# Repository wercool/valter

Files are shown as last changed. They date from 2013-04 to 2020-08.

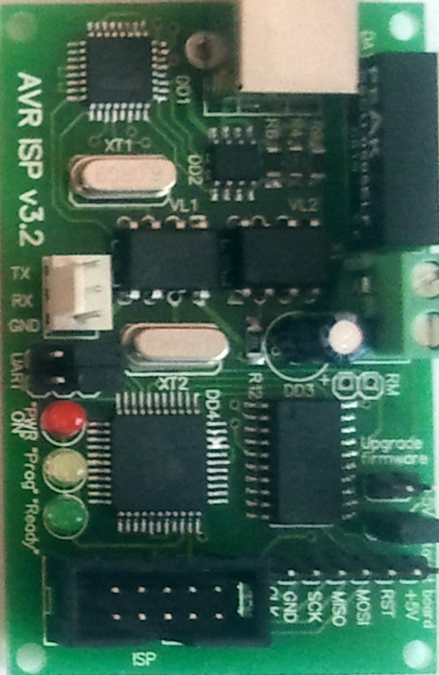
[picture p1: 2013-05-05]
mechanics/textures/avr_programmer.jpg

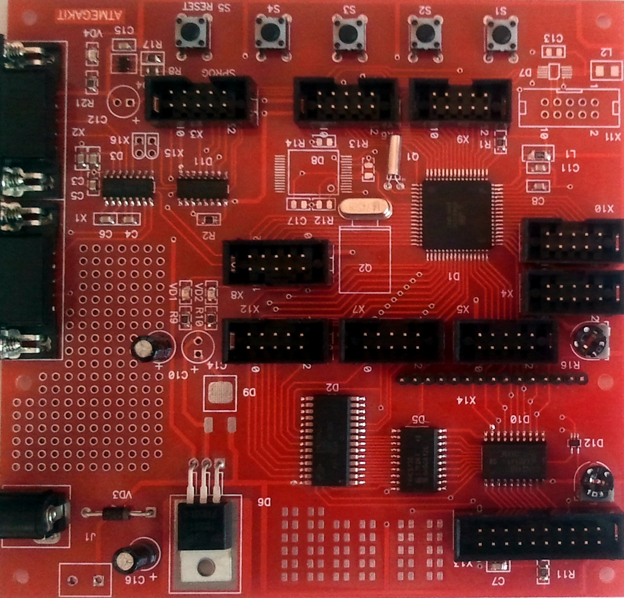
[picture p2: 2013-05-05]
mechanics/textures/mega128.jpg

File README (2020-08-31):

TRIOLAN IP: 109.87.34.156

============
Project Tree
============
cybernetics/*                               [generalized schemes, flowcharts and graphs of the whole project and it's parts, relational diagrams and schemes, etc.]
electronics/*                               [electronic and electric circuits, schemas, graphs, flowchart, abstractions, etc.]
electronics/circuits/*                      [electronic and electric principal circuits]
electronics/circuits/libcomponents/*        [Proteus library components]
electronics/circuits/libcomponents/src/*    [Proteus library components editable source Proteus files]
electronics/circuits/simulations/*          [Proteus circuits simulations]
electronics/circuits/pcb/*                  [pcb for printing and manufacturing]
electronics/flowcharts/*                    [schemas, graphs, flowchart, abstractions]
electronics/documents/*                     [data sheets on the utilized components, modules, other parts]
electronics/tables/*                        [tables of parts, pinouts, input/outputs, troubleshooting tables, etc.]
mechanics/*                                 [mechanical parts and assemblies produced in SolidWorks only]
software/*                                  [all program code assemblies and utilities, core "meta" OS, all code sources for all programmable devices like computer, microcontroller, etc.]
software/documents/*                        [miscellaneous software related documents]
software/microcontroller/*                  [microcontroller source codes and binaries]
software/microcontroller/AVR                [Atmel AVR mc source codes and binaries]
software/microcontroller/ARM                [Atmel ARM mc source codes and binaries]
software/computer/*                         [pc source codes and binaries]
software/computer/client/*                  [pc source codes and binaries - client control applications]
software/computer/client/qt                 [pc source codes for main Experimental Valter's Client Application done in Qt]
software/computer/server/*                  [pc source codes and binaries - embedded programs, core application for robot]
software/computer/server/core/*             [core application for robot (meta OS)]
software/computer/server/www/*              [web applications]

=============
Project Tools
=============
For mechanics:
1.SolidWorks 2013 x64 Edition

For electronics:
1.Proteus 7.10 SP0

For flowcharts:
1.Dia 0.97.2

For documents:
1.LibreOffice 4.0

For graphics:
1.GIMP 2

--------------------------------------------------------------------------------------------------------------------

07.10.2015 Moved to GitHub

--------------------------------------------------------------------------
07.10.2015 Confirmed
31.08.2020 Confirmed

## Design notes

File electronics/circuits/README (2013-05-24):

ussensorboard.DSN
In-home made board with US Sensors (T and R), terminal for Sharp IR distance sensor, terminals for navigation signal LEDs.

foiled fiberglass: 90x215 (2 pcs), 112x360, 37x250

platform control p1:

INPUTS:
mainAccumulatorVoltage
leftAccumulatorVoltage
rightAccumulatorVoltage
mainAccumulatorAmperageTOTAL
mainAccumulatorAmperageBOTTOM
mainAccumulatorAmperageTOP
leftAccumulatorAmperage
rightAccumulatorAmperage
chargerVoltage
leftMotorCS
rightMotorCS
turretMotorCS
turretAngle

leftMotorDIAGa
leftMotorDIAGb
rightMotorDIAGa
rightMotorDIAGb
turretMotorDIAGa
turretMotorDIAGb
leftMotorCnt
rightMotorCnt

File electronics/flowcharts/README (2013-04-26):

Platform.p1.dia
===============
Left Motor Driver
Right Motor Driver
Left Motor Optical Encoder
Right Motor Optical Encoder
Left Motor USB-Mouse Encoder
Right Motor USB-Mouse Encoder
US wall sensors
IR wall sensors

Platform.p2.dia
===============
60Ah Accumulator Sensors
5Ah Left Accumulator Sensors
5Ah Right Accumulator Sensors
Acid Accumulator Charger

Platform.cap.dia
================
Turret Motor Diver
Turret position
Left and Right sonar

Manipulator.dia
===============
Manipulator motors and sensors

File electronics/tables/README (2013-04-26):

Manipulator.ods
This file contains distribution of pins between BIT IN/OUT, ADC, and PWM targets/sources.
See electronics/flowcharts/Manipulator.dia for reference.

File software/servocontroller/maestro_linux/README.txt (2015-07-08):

Pololu Maestro USB Servo Controller Linux Software

Release Date: 2010-05-07
http://www.pololu.com/

== Summary ==

This binary release contains the Maestro Control Center
(MaestroControlCenter) and the Maestro command-line utility
(UscCmd).  These programs allow you to configure and control the
Maestro over USB.

== Prerequisites ==

You will need to download and install these packages:

  libusb-1.0-0-dev mono-runtime libmono-winforms2.0-cil

In Ubuntu, you can do this with the command:

  sudo apt-get install libusb-1.0-0-dev mono-runtime libmono-winforms2.0-cil

== USB Configuration ==

You will need to copy the file 99-pololu.rules to /etc/udev/rules.d/
in order to grant permission for all users to use Pololu USB devices.
If you already plugged in a Pololu USB device, you should unplug it at
this point so the new permissions will get applied later when you plug
it back in.

== Running the programs ==

You can run the programs by typing one of the following commands:

   ./MaestroControlCenter
   ./UscCmd

If you get an error message that says "cannot execute binary file",
then try running the program with the mono runtime, for example:

   mono ./UscCmd

== Source Code ==

The C# source code for UscCmd is available in the Pololu USB Software
Development Kit, available at:

  http://www.pololu.com/docs/0J41

== Text Display Problem in Ubuntu 9.10 ==

If you run MaestroControlCenter and some of the UI text is missing,
your problem might be caused by a bug in a graphics driver that comes
with Ubuntu 9.10 (Karmic Koala).

The driver is in the package xserver-xorg-video-intel.  The driver is
for the Intel i8xx and i9xx family of chipsets, including i810, i815,
i830, i845, i855, i865, i915, i945 and i965 series chips.  You can see
if your computer has one of those chipsets by running `lspci` and
finding your graphics card.

Version 2.9.0 of the driver is known to have a bug.
Upgrading to Version 2.9.1 seems to fix the bug.

You can determine what version of the driver you have by running:

  dpkg -l | grep xserver-xorg-video-intel

You can determine what version of the driver your X.org server is
actually using by looking in /var/log/Xorg.0.log for a message like:

  (II) Module intel: vendor="X.Org Foundation"
          compiled for 1.6.4, module version = 2.9.1
          Module class: X.Org Video Driver
          ABI class: X.Org Video Driver, version 5.0

One way to fix the problem is to compile the new version of the driver
(2.9.1) from source and use it.  Here are the instructions for doing
that:

1) Go to http://xorg.freedesktop.org/archive/individual/driver/
   and get the latest version of the xf86-video-intel driver.
   At the time of this writing (2009-12-23), the latest version
   was xf86-video-intel-2.9.1.tar.gz.

2) Unzip the archive and install the archive by running:

     tar -xzvf xf86-video-intel-2.9.1.tar.gz

3) Install the required dev packages:

     sudo apt-get install xserver-xorg-dev libdrm-dev x11proto-gl-dev x11proto-xf86dri-dev

4) Install the driver by running:

     cd xf86-video-intel-2.9.1
     ./configure
     make
     sudo make install

   This installs the drivers to /usr/local/lib/xorg/modules/drivers,
   but that is not the location where the X.org server searches for
   drivers.

5) (Optional) Make a backup up the existing drivers so that if
   something goes wrong you can revert to them:
     cp -Ri /usr/lib/xorg/modules/drivers ~/backup_xorg_drivers
 
6) Close all of your graphical applications and log out because we must
   temporarily shut down the Gnome Desktop Manager (gdm).

7) Go to a text console by pressing Ctrl+Alt+F1 or Ctrl+Alt+F2.

8) Run these commands:
     sudo service gdm stop
     sudo cp /usr/local/lib/xorg/modules/drivers/* /usr/lib/xorg/modules/drivers
     sudo service gdm start

9) You should see the Ubuntu log-in screen appear.  If it does not, try
   pressing Ctrl+Alt+F7.  The graphic driver bug should now be fixed!

For more information, see:
https://bugzilla.novell.com/show_bug.cgi?id=549882
https://bugs.launchpad.net/ubuntu/+source/xserver-xorg-video-intel/+bug/462349
http://intellinuxgraphics.org/

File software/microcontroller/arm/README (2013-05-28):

On 64 bits version install 32 bits libraries: 

apt-get install ia32-libs

==============

ia32-libs - ia32 shared libraries - transitional package
ia32-libs-multiarch - Multi-arch versions of former ia32-libraries

Useful links:

AT91 ARM-Projects
http://www.siwawi.arubi.uni-kl.de/avr_projects/arm_projects/index_at91.html

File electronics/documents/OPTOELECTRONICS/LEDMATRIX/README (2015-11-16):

missed dimension on the drawing: 24.6mm (between pins axis - 24.1mm)

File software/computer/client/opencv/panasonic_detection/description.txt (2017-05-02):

Panasonic Wireless Phone
cascade_r.xml=Right Oriented
cascade_l.xml=Left Oriented
cascade_t.xml=Top Oriented
cascade_b.xml=Bottom Oriented

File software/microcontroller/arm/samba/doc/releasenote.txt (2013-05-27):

Release Notes ¡V SAM-BA
-----------------------
Release version: 2.11
Release date: 2011

1 Overview

The SAM Boot Assistant (SAM-BA) software provides a means of easily 
programming different Atmel AT91SAM devices. They are based on a common 
dynamic linked library (DLL), the sam-ba.dll. SAM-BA use the DLL to 
communicate with the target board.

You are strongly recommended to read through the following release notes 
before completing the installation of SAM-BA v2.11.

AT91BOOT_DLL.DLL and SAM-PROG is not updated in this revision. 
SAM-PROG will remain available in  the at91isp v1.13. 
Customer who still wants SAM-PROG can download AT91-ISP v1.13.

----------
2 Downloading and Installing
----------------------------
The software can be found and downloaded from ATMEL's website at 
http://www.atmel.com/dyn/products/tools_card_v2.asp?tool_id=3883
  
- sam-ba_2.11.exe (current release) for Windows
  Install files for the SAM-BA package. 
  Execute sam-ba_2.10.exe to install. 
  
- sam-ba_2.11.zip (current release) for Linux
  Install files for the SAM-BA package only. Uses standard CDC driver
  Unzip the package zip file under a local folder on your PC.

3 Contents
-----------

- sam-ba.dll v1.00 (A dynamic linked library connects AT91SAM-based targets 
  through a USB, JTAG or COM port).

- Segger JLINKARM.DLL V4.28b (DLL for using J-Link / J-Trace with third-party 
  programs JTAG driver)

- TCL Toolchain including tclsh can be downloaded from the following URL:
  http://www.activestate.com/Products/ActiveTcl/

- Documents
  - SAM-BA User Guide.pdf
  - Releasenote.txt
  - readme.txt
  - usb_notice.html

- New features.
  - at91sam3s8 at91sam3s16 support
  - at91sam3x8 at91sam3x4 at91sam3x2 support
  - at91sam9g15 at91sam9g25 at91sam9g35 at91sam9x25 at91sam9x35 support
  - at91sam9n12 support

- SAMBA 2.11 supports the following AT91SAM based microcontrollers:
  - at91sam3s16 at91sam3s8 at91sam3s4 at91sam3s2 at91sam3s1
  - at91sam3u4 at91sam3u2 at91sam3u1
  - at91sam3n4 at91sam3n2 at91sam3n1
  - at91sam3x8 at91sam3x4 at91sam3x2
  - at91sam7a3
  - at91sam7l64 at91sam7l128     
  - at91sam7s161 at91sam7s321 at91sam7s32 at91sam7s64 at91sam7s128 at91sam7s256 at91sam7s512
  - at91sam7se32 at91sam7se256 at91sam7se512
  - at91sam7x128 at91sam7x256 at91sam7x512
  - at91sam7xc128 at91sam7xc256 at91sam7xc512
  - at91sam9260 
  - at91sam9261
  - at91sam9263
  - at91sam9g10
  - at91sam9g15 at91sam9g25 at91sam9g35 at91sam9x25 at91sam9x35
  - at91sam9n12
  - at91sam9g20
  - at91sam9g45
  - at91sam9m10 
  - at91sam9rl64
  - at91sam9xe128
  - at91sam9xe128
  - at91sam9xe256
  - at91sam9xe512
  - at91cap9

4 Bug Fixes and Enhancement
----------------------------
Enhancement:
------------
    - Support USB CDC, JLINK and COM port connection for Vista (32/64) and Windows 7 (32/64)
    - Upgrade to Tcl8.5.9 / Tk8.5.9  (samba 2.10 Tcl8.4.13 / Tk8.4.13)
    - new sam-ba.dll instead of SAMBA_DLL.DLL
    - using usbser.sys(Microsoft Windows USB modem driver system driver file)
      instead of atm6124.sys
    - nandflash applet : Remove RDY/BSY pin usage for SAM-BA
    - remove DDRAM duplicated configurations in board_memories.c 
    - Remove duplicated tcl_lib folder
    - SAM9M10/G45 coherency
    - Add One Wire EEPROM support for sam9x5 series
    - SST Serial Flash support
    - backup connection information and last used folder as soon as sam-ba used
    - add a mask on revision field in JEDEC ID to be able to support several
      version of a given flash
    - Add support of modern Embedded Linux file systems(ubifs / yaffs2 / jffs2 support)
    - Add Jlink speed interface
    - Name of USB serial link
    - TWI Address optional selection for EEPROM (9g15/9g25/9g35/9x25/9x35/9n12)
    - Support /dev/ttyACMx for Linux version samba

Bug Fixes
---------
    - sam3s lowlevel init prevents the user to use a crystal different 
      from 12 MHz
    - the external XTtal shall NOT be enabled for sam9m10
    - descriptor error for SST Serial Flash
    - File compare (>10K) not matched though COM port
    - serial flash driver bug fix
    - sam7x256 flash applet does not write using IAP ROM feature
    - fixed sam7 with IAP flash loader issue
    - fixed sam9m10-g45-ek board_lowlevelinit issue
    - The customer should be allowed to use it's real board name
    - reduce the erase size of serialflash applet
    - No adaptive clocking for SAM3 devices
    - sam7x512 Flash Erase command does not work for the 2nd flash bank
    - Assembly code (in old applets) compilation
    - Wrong lowlevel inits for sam3x applets 
    - Cap9 SDRAM (extram) applet linker script issue
    - Buffer size issue in example samba_dll_usage_VC6
    - Miss "rc" indication in installer, folders and inside the program
    - SAM-BA installer no admin right to install on WIN7 /Vista
    - SAM-BA crashes when no_board selection.
    - SDRAM and DDRAM panes shall not be displayed at the same time in the GUI
    - Nandflash applet debug incorrect info of SEND BOOT FILE
    - Incorrect board name displayed in main window (some board re-target)
    - SAM9G15-ES2 : Cannot be launched twice without cpu reset
    - Name of sam9x25 / x35 tcl files (devices) shall be lowercase
    - TCL scan crash in some case for linux sam-ba
    - After a TCL_Go, If the applet does not return, SAM-BA is frozen.
    - Incorrect board name displayed in main window (some board re-target)
    - Sam9n12 applet compile error in linux
    - Missing ACK for COM connection in extram and lowlevel applet for 9xx5/9n12
    
Known Issues
---------
    - Some boards can't work properly through USB/COM port connection without reseting the board
----------------------------------------------------------------------------------------------------------------------------------

5 History 
---------------------

----------------------------------------------------------------------------------------------------------------------------------
v2.10:
    - Fixed Jtag issue when the chip has booted on a program from an external memory (Nand, DF ...) and if that program has initialized the PLL and MCK. 
    - Fixed Jtag issue if customers not running the chips with the same XTAL or external oscillator as on our EK boards.
    - Add new at25 device AT25DF512B-SSH-B,AT25DF021-SSH-B,AT25DF021-MH-T,AT25DF161-SSH-B,AT25DF161-SH-B,AT25DF641-S3H-B.
    - Fixed flash init problem on AT91SAM7S32/321.
    - Fixed DataFlash init problem on AT91SAM7A3.
    - Fixed dataFlash programming of large files fails (~>1Mbytes) on AT91SAM9G20 with COM port connection.
    - Fixed flash applet initialization in CDC mode on SAM7.
    - Fixed SAM7X/XC access cdc linux , Flash init fail with error message.
    - Add "Send Boot File" for SAM9G10/G20/G45/M10 chips.
    - Add lowlevel_init in flash applet for sam7 chip.
    - Fix spell error "appletMAilboxAddr" at91sam7s128-ek.tcl.
    - Fix security bit script for at91sam3u4-ek.tcl.
    - Fixed  Nand flash program algorithm for SAM9M10/9G45.
    - When using the JTAG it is not possible to program the 2nd flash bank of the SAM7X512 device.
    - Fixed flash init problem on AT91SAM7S32/321.
    - Add support to verify if an existing sam-ba task is running before launching sam-ba, ask to kill it.
    - No Support for 8-bit Nand Small Blocks. The algorithm is not correctly implemented for such nandflash devices.
    - An incorrect EEPROM::appletAddr in TCL definitions address to SDRAM could lead to crash for some at91sam9 boards.
    - The applet initialization does not report any error in case no EEPROM is connected or an EEPROM different from the selected one 
      is Enabled by the script.
    - Latest large nandflash devices have bigger page size (4K for instance) and SAMBA and the SW library does not support it. This 
      may be due to the new spare zone organization.
    - An incorrect 'Enable Security Bit' descriptor for SAM3U.
    - Add function to erase blocks for NAND flash applet (command line only)
    - NOR flash not able to 'erese all' on sam9m10-g45-ek REV.A board
    - When SAM-BA starts, it could not differentiate a real invalid ID from a communication error with the chip.
    - Sam-ba could not detect real board, if user select a wrong board name from drop list.
    - It is not possible to connect to SAMBA with a SAM9260-EK using the RS232 port.
    - Some customer board could not program dataflash properly, improve the programming algorithm.
    - Improved erase all algorithm for nandflash applet. Fixed Usb/com timeout problem on some 8-Bit Nand flash.
    - Fixed eeprom program algorithm for SAM9260-EK.
    - Add Dataflash (SPI0 CS3) support for SAM9261-EK.
    - Flash applet in command mode could not unlock region before write.
    - Fixed connection on SAM3S-EK with COM port.
    - CDC version hang during flash init of SAM7 chips.
    - Connect/disconnect functionality support.

----------------------------------------------------------------------------------------------------------------------------------
v2.9:
    - Added support for AT91SAM9M10, AT91SAM9G45, AT91SAM9G10, AT91SAM7SL.
    - Added support for AT91SAM3U, with USB and COM port connection only (no SAM-ICE).
    - Fixed Dataflash access on AT91SAM9G20 CU-A.
    - Select 16/32 bits external SDRAM in board TCL file without applet compilation.
    - External memory initialization failure at SAM-BA startup is indicated by a popup
       window, but user can choose to use SAM-BA anyway.
    - Added a listbox to choose applet debug traces level easily. Traces are sent to DBGU
       port when using USB or JTAG connection link.
    - Added Nandflash bad block listing script.
    - Added a document to help user to customize SAM-BA and applets for a custom board.

----------------------------------------------------------------------------------------------------------------------------------
v2.8:
    - Added support for DataFlash in Binary mode (Power of 2 page size),
    - Improved programing speed with applets running at higher CPU and MCK clock frequency,
    - Fixed AT91SAM7L64/128 support,
    - Fixed AT91SAM7XC support.

----------------------------------------------------------------------------------------------------------------------------------
v2.7:
    - New flash programming applets :
        - NandFlash, DataFlash, SerialFlash, NorFlash,
        - GCC code,
        - based on at91lib software library. 
    - Added support for AT91SAM7L64/128, AT91SAM9G20, AT91SAM9XE,
        and AT91CAP9 (EK and STK).
    - Fixed AT91SAM9RL64 support.

----------------------------------------------------------------------------------------------------------------------------------
v2.6:
    - Fixed AT91SAM9263 DataFlash script bug.
    - Fixed AT91SAM7S512/SE512/X512 Flash programming bug.
    - Fixed AT91SAM7SE/X/XC GPNVM accesses with JTAG.
    - Added support for AT91SAM9RL64 and AT91CAP9.
    - More NandFlash supported :
        * Micron, Samsung, Toshiba, Fujitsu, National, and STMicro
        * 1Gbit to 16Gbits, 8 and 16 bits bus size.
    - Improved NandFlash bad block management (Skip block method).
    - JTAG support for AT91SAM926x.

----------------------------------------------------------------------------------------------------------------------------------
v2.5:
    - Bypass of Connection Message Box when launching SAM-BA with port
       and board name in command line parameter.
    - Support for AT91SAM9XE family.
    - Various bug fixes : script mode feature improved (no more message boxes),
       open and save file dialog boxes displays now correctly.

----------------------------------------------------------------------------------------------------------------------------------
v2.4:
    - J-Link support improved for AT91SAM7A3
    - AT91SAM9263 NandFlash block programming support
    - Added SDRAM config for 48, 100 and 133 MHz MCK on SAM926x boards
    - Minor GUI bug fixes

----------------------------------------------------------------------------------------------------------------------------------
v2.3:
    Supports:
    - SAM7S32/321/64/128/256/512
    - SAM7X(C)128/256/512
    - SAM7SE32/256/512
    - SAM9260/9261/9263
    Only by adding/modifying TCL scripts in the lib directory, it is now
      possible to add:
    - Your own boards
    - Your own memory algorithms
----------------------------------------------------------------------------------------------------------------------------------

6 Contact Information
---------------------
For support on the AT91 Software Package please send request to at91@atmel.com

---------------------
6 Copyright (c) 2011, Atmel Corporation All rights reserved.

 * ----------------------------------------------------------------------------
 *         ATMEL Microcontroller Software Support
 * ----------------------------------------------------------------------------
 * Copyright (c) 2011, Atmel Corporation
 *
 * All rights reserved.
 *
 * Redistribution and use in source and binary forms, with or without
 * modification, are permitted provided that the following conditions are met:
 *
 * - Redistributions of source code must retain the above copyright notice,
 * this list of conditions and the disclaimer below.
 *
 * Atmel's name may not be used to endorse or promote products derived from
 * this software without specific prior written permission.
 *
 * DISCLAIMER: THIS SOFTWARE IS PROVIDED BY ATMEL "AS IS" AND ANY EXPRESS OR
 * IMPLIED WARRANTIES, INCLUDING, BUT NOT LIMITED TO, THE IMPLIED WARRANTIES OF
 * MERCHANTABILITY, FITNESS FOR A PARTICULAR PURPOSE AND NON-INFRINGEMENT ARE
 * DISCLAIMED. IN NO EVENT SHALL ATMEL BE LIABLE FOR ANY DIRECT, INDIRECT,
 * INCIDENTAL, SPECIAL, EXEMPLARY, OR CONSEQUENTIAL DAMAGES (INCLUDING, BUT NOT
 * LIMITED TO, PROCUREMENT OF SUBSTITUTE GOODS OR SERVICES; LOSS OF USE, DATA,
 * OR PROFITS; OR BUSINESS INTERRUPTION) HOWEVER CAUSED AND ON ANY THEORY OF
 * LIABILITY, WHETHER IN CONTRACT, STRICT LIABILITY, OR TORT (INCLUDING
 * NEGLIGENCE OR OTHERWISE) ARISING IN ANY WAY OUT OF THE USE OF THIS SOFTWARE,
 * EVEN IF ADVISED OF THE POSSIBILITY OF SUCH DAMAGE.
 * ----------------------------------------------------------------------------

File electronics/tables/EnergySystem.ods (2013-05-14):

BIT IN | 5 | 5 from SM 1236 charger
BIT OUT | 6
ADC | 3

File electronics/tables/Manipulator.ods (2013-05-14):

BIT IN | 1
BIT OUT | 14
ADC | 8 | 7 in case of series connection of left upper right sensors
PWM | 3 (4) | 4 in case of camera servo control from mc

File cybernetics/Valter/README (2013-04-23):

http://en.wikipedia.org/wiki/Cybernetics
http://ru.wikipedia.org/wiki/Кибернетика

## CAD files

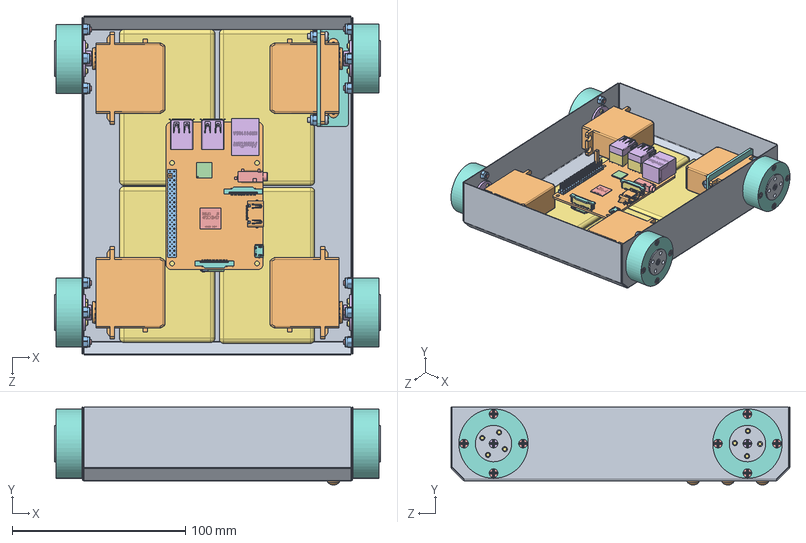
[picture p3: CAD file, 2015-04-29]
documents/GB-0814/mechanics/GB0814.SLDASM
188.0 x 44.8 x 195.4 mm
case.bottom
SM4315R x 4
raspberry_pi_B+_(bar_180_2x20)
raspberry_pi_B+_(QFN64)
raspberry_pi_B+_(168_FBGA_12x12)
raspberry_pi_B+_(USB_x2_part1) x 2
raspberry_pi_B+_(USB_x2_part2) x 2
raspberry_pi_B+_(micro_USB_cover)
raspberry_pi_B+_(micro_USB_contacts)
raspberry_pi__HDMI_socket_cover
raspberry_pi__HDMI_socket_inside
raspberry_pi__HDMI_socket_large_pin x 10
raspberry_pi__HDMI_socket_small_pin x 9
raspberry_pi_B+_(RJ45)
raspberry_pi__15_pin_FFC_Connector_body x 2
raspberry_pi__15_pin_FFC_Connector_locker x 2
raspberry_pi__15_pin_FFC_Connector_pins x 30
raspberry_pi_B+_(CI_Board)
raspberry_pi_B+_(microsd_slot2)
raspberry_pi_B+_(microsd2)
raspberry_pi_B+_(audio_video2)
SM4315R.horn x 4
accumulator x 4
flange x 4
wheel.hub x 4
pin.2.54.holder
self.stop.nut.m3 x 20
ball.4mm x 152
m3.screw.18mm x 16
m3.screw.30mm x 4
m2.screw x 16
servo.fixture
m3.screw.10mm x 4
4mm.rivet x 3

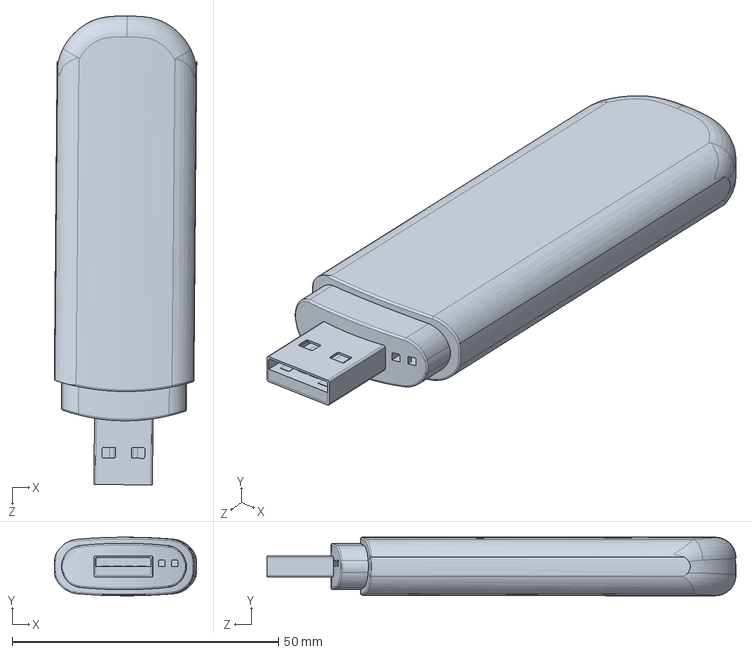
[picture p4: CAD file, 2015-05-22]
documents/misc/GB-0814/mechanics/3gmodem/3gmodem.SLDASM
26.7 x 11.0 x 88.0 mm

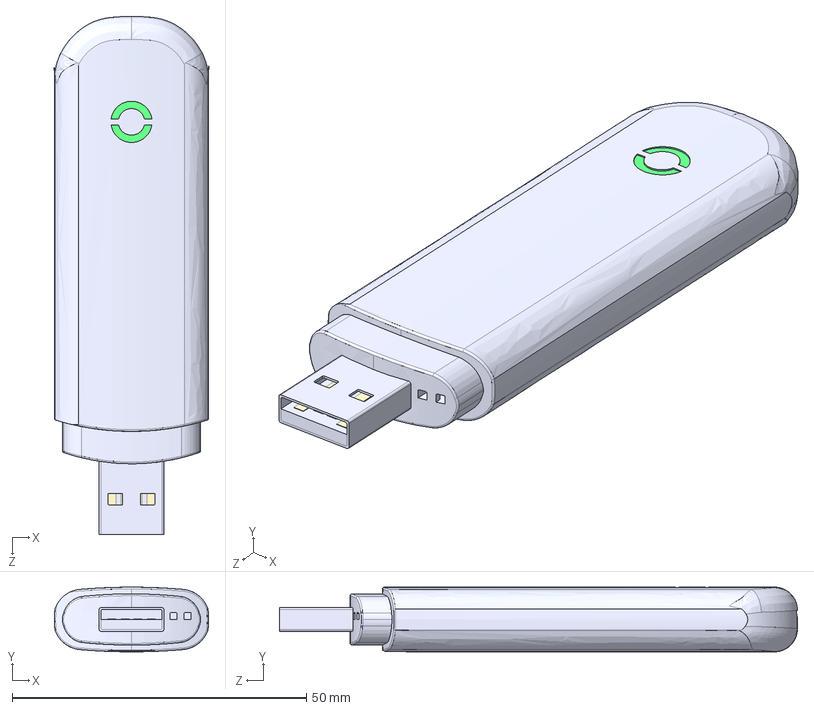
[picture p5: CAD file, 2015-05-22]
documents/misc/GB-0814/mechanics/3gmodem/IGES Files/Main_IGES.IGS
26.2 x 11.0 x 88.0 mm

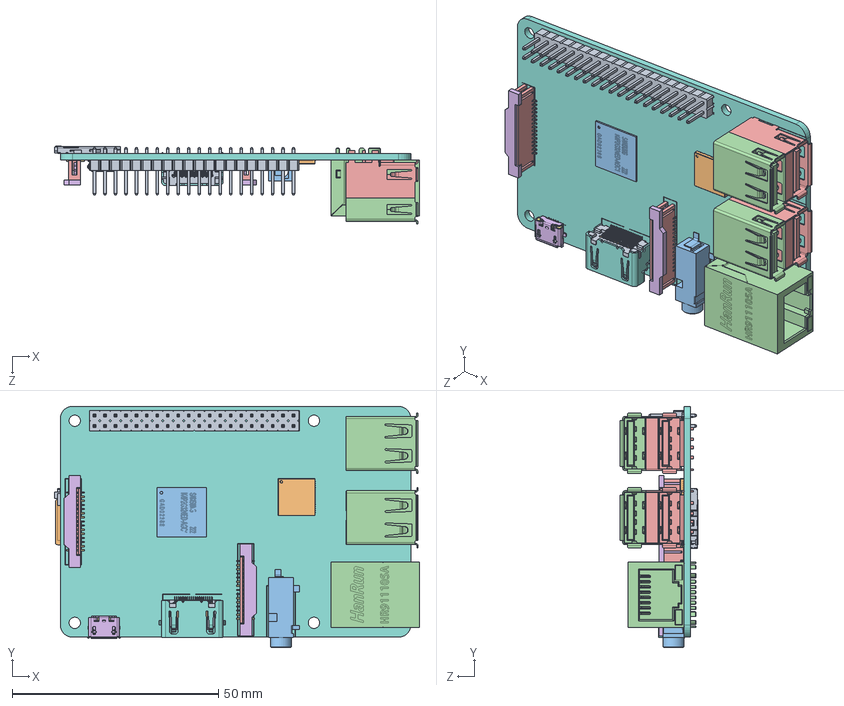
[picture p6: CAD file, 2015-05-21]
documents/misc/GB-0814/mechanics/raspberry-pi-model-b-2/raspberrypi_b_+_(assembly).SLDASM
88.5 x 58.5 x 18.9 mm
raspberry_pi_B+_(bar_180_2x20)
raspberry_pi_B+_(QFN64)
raspberry_pi_B+_(168_FBGA_12x12)
raspberry_pi_B+_(USB_x2_part1) x 2
raspberry_pi_B+_(USB_x2_part2) x 2
raspberry_pi_B+_(micro_USB_cover)
raspberry_pi_B+_(micro_USB_contacts)
raspberry_pi__HDMI_socket_cover
raspberry_pi__HDMI_socket_inside
raspberry_pi__HDMI_socket_large_pin x 10
raspberry_pi__HDMI_socket_small_pin x 9
raspberry_pi_B+_(RJ45)
raspberry_pi__15_pin_FFC_Connector_body x 2
raspberry_pi__15_pin_FFC_Connector_locker x 2
raspberry_pi__15_pin_FFC_Connector_pins x 30
raspberry_pi_B+_(CI_Board)
raspberry_pi_B+_(microsd_slot2)
raspberry_pi_B+_(microsd2)
raspberry_pi_B+_(audio_video2)

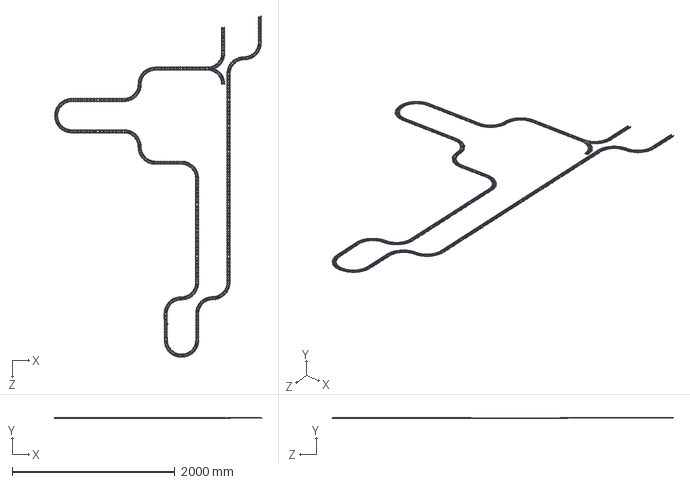
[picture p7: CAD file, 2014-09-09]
documents/misc/railway/railway.SLDASM
2545.2 x 6.78 x 4186.4 mm
linear.rail x 23
radius.rail x 17

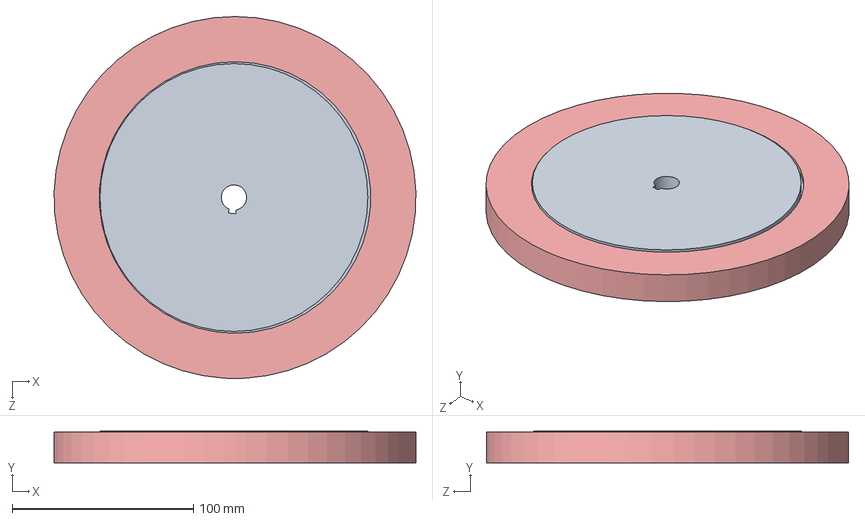
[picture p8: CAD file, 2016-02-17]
mechanics/turret.SLDASM
199.9 x 17.6 x 200.0 mm
turret-p1
turret-p2 x 17
turret-p3
turret-p5 x 100
turret-p4

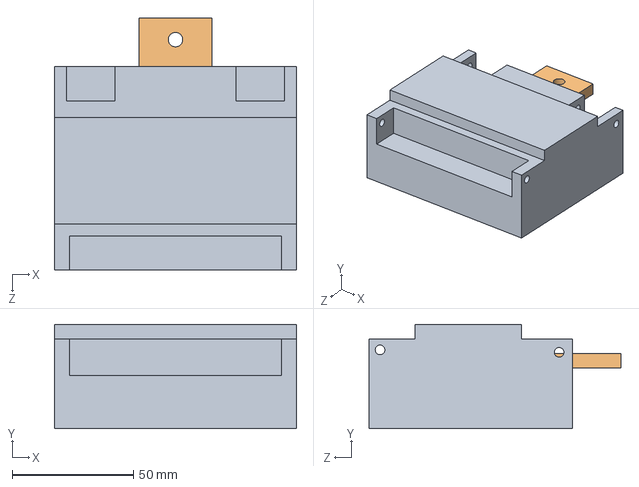
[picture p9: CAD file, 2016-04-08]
software/ros/misc/models/valter/swmodel/palm.SLDASM
100.0 x 43.0 x 104.0 mm
palm
palm.p1

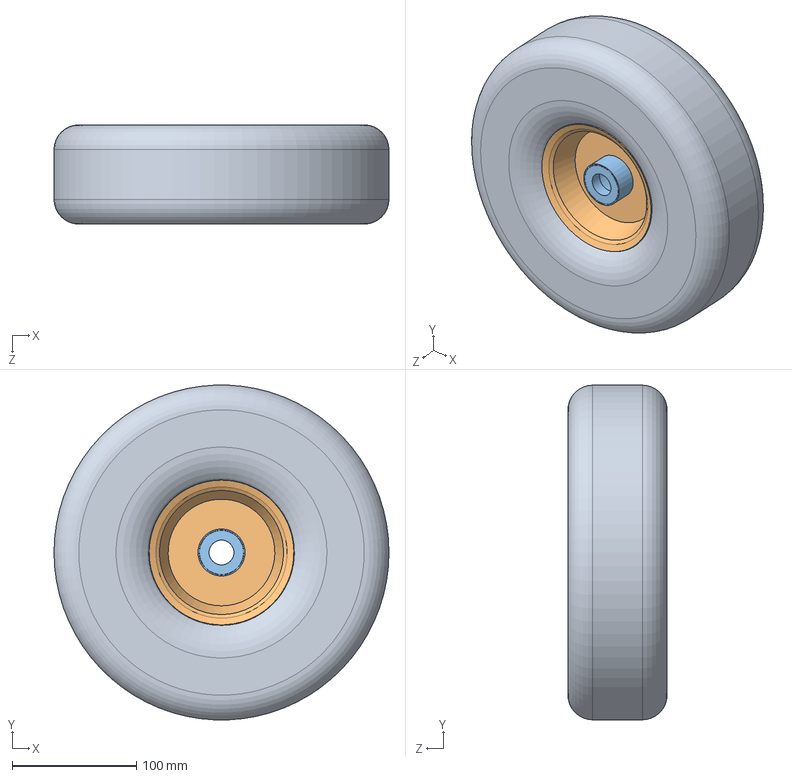
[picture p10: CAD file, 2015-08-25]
software/ros/misc/models/valter/swmodel/wheel/wheel.SLDASM
270.0 x 269.8 x 80.0 mm
wheel.chamber
wheel.metal.front
wheel.metal.internal

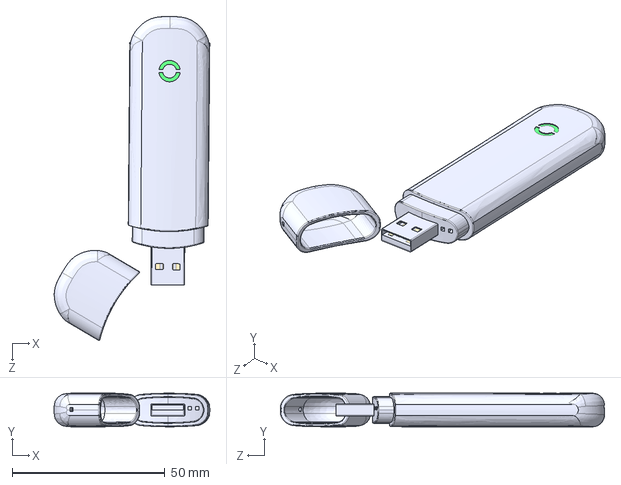
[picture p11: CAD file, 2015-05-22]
documents/misc/GB-0814/mechanics/3gmodem/IGES Files/Dongle Assembly_IGES.IGS
51.0 x 11.0 x 106.2 mm

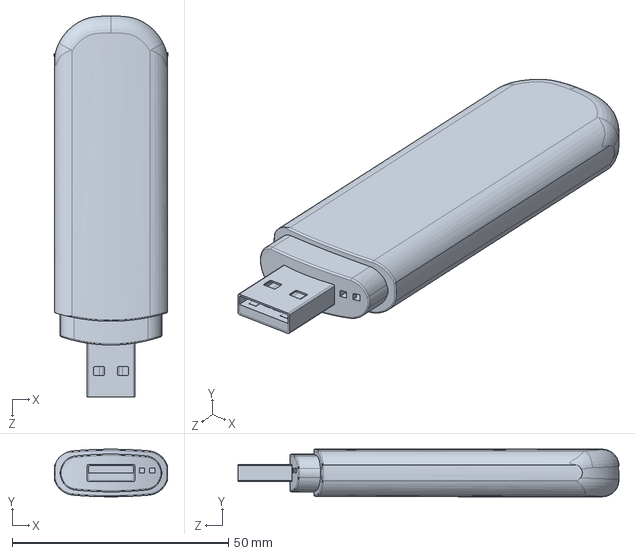
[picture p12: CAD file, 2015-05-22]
documents/misc/GB-0814/mechanics/3gmodem/Main.SLDPRT
26.2 x 11.0 x 88.0 mm

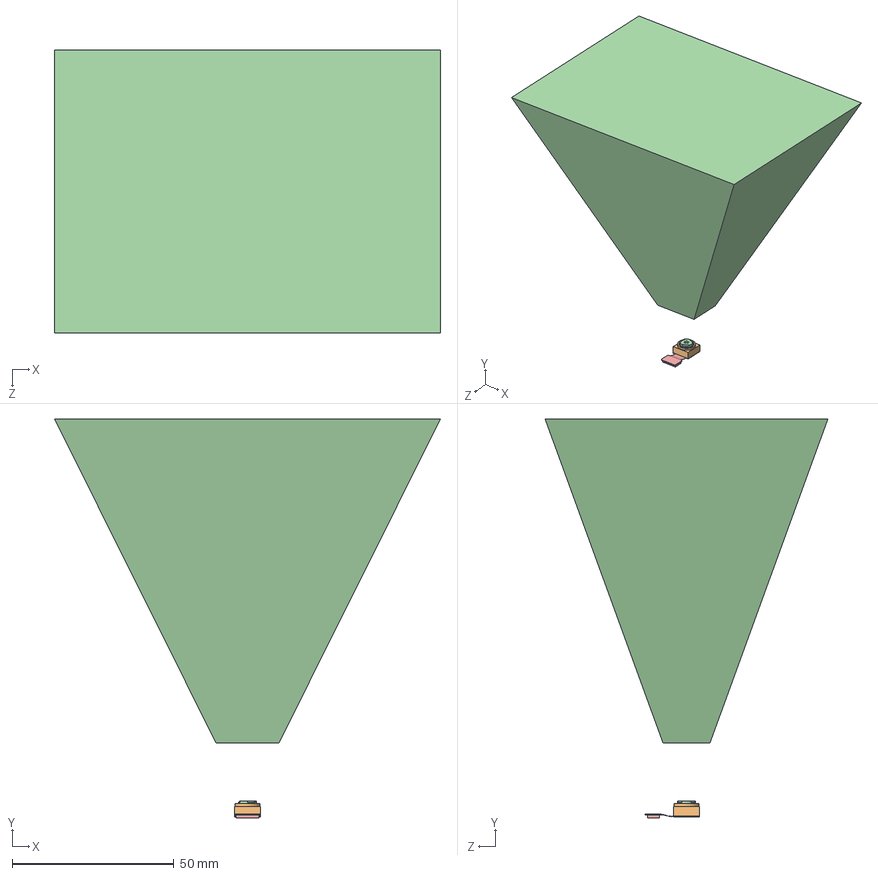
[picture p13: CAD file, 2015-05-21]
documents/misc/GB-0814/mechanics/raspberry-pi-camera/OVA5647.SLDASM
119.2 x 123.2 x 87.4 mm
OVA5647
OVA5647_Housing
OVA5647_IR-Glas
OVA5647_Lens
OVA5647_Pigtail

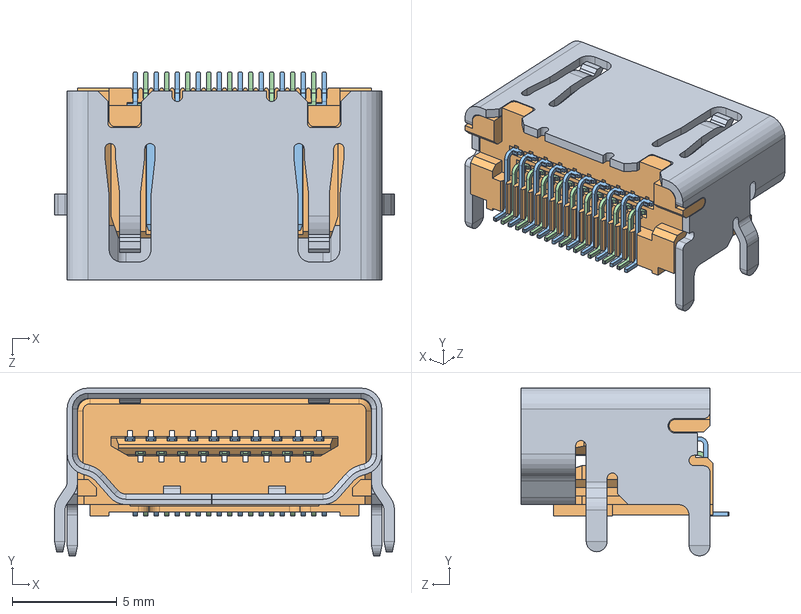
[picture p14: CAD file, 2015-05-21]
documents/misc/GB-0814/mechanics/raspberry-pi-model-b-2/raspberry_pi_B+_(HDMI_socket).SLDASM
16.2 x 8.00 x 9.90 mm
raspberry_pi__HDMI_socket_cover
raspberry_pi__HDMI_socket_inside
raspberry_pi__HDMI_socket_large_pin x 10
raspberry_pi__HDMI_socket_small_pin x 9

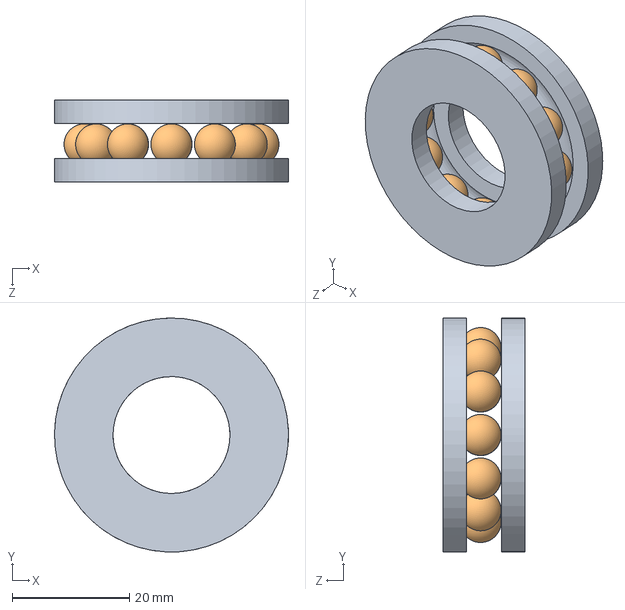
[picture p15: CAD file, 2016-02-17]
mechanics/wheel.stop.bearing.SLDASM
40.0 x 40.0 x 14.0 mm
wheel.stop.bearing.p1 x 2
wheel.stop.bearing.p2 x 12

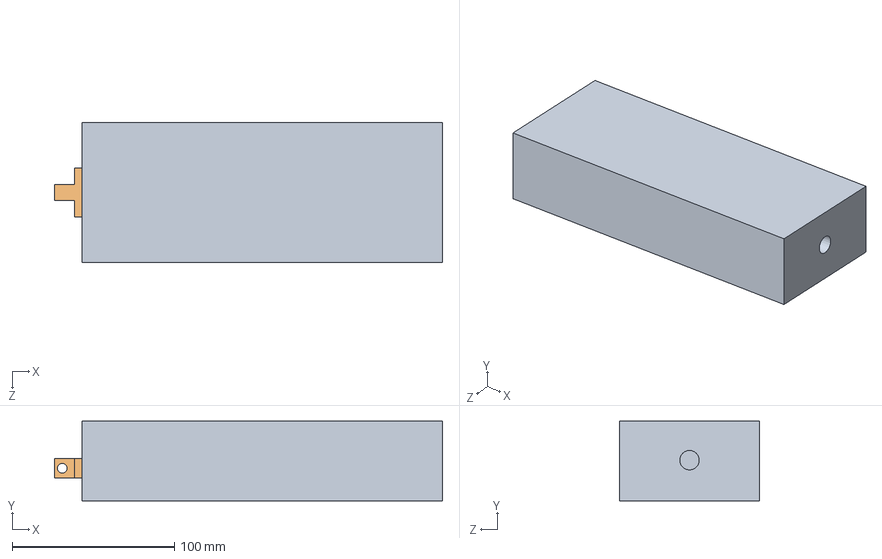
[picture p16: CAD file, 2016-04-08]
software/ros/misc/models/valter/swmodel/forearm.SLDASM
239.0 x 49.0 x 86.0 mm
forearm.p2
palm.lift.fixture

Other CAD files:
documents/misc/GB-0814/mechanics/3gmodem/STL Files/Main_STL.STL
software/ros/misc/models/valter/swmodel/wheel.support/wheel.support.SLDASM
documents/misc/GB-0814/mechanics/3gmodem/Dongle Assembly.SLDASM
documents/misc/GB-0814/mechanics/LEDLamp/LEDLamp.SLDASM
documents/misc/GB-0814/mechanics/3gmodem/Dongle Assembly_AS PART.SLDPRT
documents/misc/GB-0814/mechanics/3gmodem/IGES Files/Lid_IGES.IGS
documents/misc/GB-0814/mechanics/3gmodem/Lid.SLDPRT
documents/misc/GB-0814/mechanics/3gmodem/STL Files/Lid_STL.STL
documents/misc/GB-0814/mechanics/4mm.rivet.SLDPRT
documents/misc/GB-0814/mechanics/4mmx4mm.rivet.SLDPRT
documents/misc/GB-0814/mechanics/4mmx8mm.rivet.SLDPRT
documents/misc/GB-0814/mechanics/LEDLamp/housing.SLDPRT
documents/misc/GB-0814/mechanics/LEDLamp/ledlampnut.SLDPRT
documents/misc/GB-0814/mechanics/SM4315R.SLDPRT
documents/misc/GB-0814/mechanics/SM4315R.horn.SLDPRT
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

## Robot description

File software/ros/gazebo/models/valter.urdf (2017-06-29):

<robot name="valter">
  <link name="Base">
    <inertial>
      <origin xyz="-0.0831283905237907 -8.99639602360447E-05 0.418094636104011" rpy="0 0 0" />
      <mass value="50.0" />
      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
    </inertial>
    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
  </link>
  <link name="RWheel">
    <inertial>
      <origin xyz="-5.908901840046E-18 -0.04 2.77555756156289E-17" rpy="0 0 0" />
      <mass value="3.62031355964479" />
      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
    </inertial>
    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
  </link>
  <joint name="RWheelJoint" type="fixed">
    <origin xyz="0.000341577688738742 -0.153675665570238 0.14" rpy="-6.12303176911189E-17 0 0" />
    <parent link="Base" />
    <child link="RWheel" />
    <axis xyz="0 1 0" />
  </joint>
  <link name="rwheel_centers">
    <inertial>
      <origin xyz="-8.13151629364128E-19 0.032994484499226 0" rpy="0 0 0" />
      <mass value="0.0783773140784392" />
      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
    </inertial>
    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
  </link>
  <joint name="rwheel_centers_fixed" type="fixed">
    <origin xyz="0 -0.00181724367610836 0" rpy="3.14159265358979 0 0" />
    <parent link="RWheel" />
    <child link="rwheel_centers" />
    <axis xyz="0 0 0" />
  </joint>
  <link name="LWheel">
    <inertial>
      <origin xyz="-2.77555756156289E-17 -0.04 2.77555756156289E-17" rpy="0 0 0" />
      <mass value="3.62031355964479" />
      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
    </inertial>
    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
  </link>
  <joint name="LWheelJoint" type="fixed">
    <origin xyz="0.000341577688738742 0.154324334429763 0.14" rpy="6.6286088844449E-17 0.39309481042652 -3.14159265358979" />
    <parent link="Base" />
    <child link="LWheel" />
    <axis xyz="0 -1 0" />
  </joint>
  <link name="lwheel_centers">
    <inertial>
      <origin xyz="-6.93889390390723E-18 -0.032994484499226 -2.77555756156289E-17" rpy="0 0 0" />
      <mass value="0.0783773140784395" />
      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
    </inertial>
    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
  </link>
  <joint name="lwheel_centers_fixed" type="fixed">
    <origin xyz="0 -0.00181724367610836 0" rpy="0 -1.66371525153719E-34 0" />
    <parent link="LWheel" />
    <child link="lwheel_centers" />
    <axis xyz="0 0 0" />
  </joint>
  <link name="support_wheels">
    <inertial>
      <origin xyz="-0.219066879644595 -1.38777878078145E-17 -0.111817164878115" rpy="0 0 0" />
      <mass value="1.30791131979034" />
      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
    </inertial>
    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
  </link>
  <joint name="support_wheels_fixed" type="fixed">
    <origin xyz="0.189234607270609 -0.11129709785824 0.0679256801186866" rpy="1.5707963267949 0 0" />
    <parent link="Base" />
    <child link="support_wheels" />
    <axis xyz="0 0 0" />
  </joint>
  <link name="support_wheels_centers">
    <inertial>
      <origin xyz="-0.219066879644595 -2.77555756156289E-17 0.110556114336065" rpy="0 0 0" />
      <mass value="0.101015328916835" />
      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
    </inertial>
    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
  </link>
  <joint name="support_wheels_centers_fixed" type="fixed">
    <origin xyz="0 0 -0.222438597166117" rpy="0 0 0" />
    <parent link="support_wheels" />
    <child link="support_wheels_centers" />
    <axis xyz="0 0 0" />
  </joint>
  <link name="ManipulatorBase">
    <inertial>
      <origin xyz="0.0757274431880703 -0.00904190076144362 -0.035" rpy="0 0 0" />
      <mass value="0.178834143520891" />
      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
    </inertial>
    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
  </link>
  <joint name="ManipulatorBaseFixed" type="fixed">
    <origin xyz="0.15727 0.035461 0.70704" rpy="1.5708 0 3.1416" />
    <parent link="Base" />
    <child link="ManipulatorBase" />
    <axis xyz="0 0 0" />
  </joint>
  <link name="ManipulatorLink1">
    <inertial>
      <origin xyz="0.00842708530014899 -0.298874962931971 0.0349954696862612" rpy="0 0 0" />
      <mass value="0.478012742893284" />
      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
    </inertial>
    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
  </link>
  <joint name="ManipulatorLink1Joint" type="revolute">
    <origin xyz="0.015824 -0.0090419 0" rpy="3.1416 0 3.1416" />
    <parent link="ManipulatorBase" />
    <child link="ManipulatorLink1" />
    <axis xyz="0 0 -1" />
    <limit lower="-1.5" upper="0" effort="0" velocity="0" />
  </joint>
  <link name="ManipulatorLink2">
    <inertial>
      <origin xyz="-0.00196480942981017 0.348379096758467 0.0349954207736472" rpy="0 0 0" />
      <mass value="0.304515245459477" />
      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
    </inertial>
    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
  </link>
  <joint name="ManipulatorLink2Joint" type="revolute">
    <origin xyz="0.10656 -0.49054 0" rpy="0 0 0" />
    <parent link="ManipulatorLink1" />
    <child link="ManipulatorLink2" />
    <axis xyz="0 0 -1" />
    <limit lower="0" upper="1.5" effort="0" velocity="0" />
  </joint>
  <link name="ManipulatorLink3">
    <inertial>
      <origin xyz="-0.0046525999175398 -0.0219448226910157 0.0349954293087308" rpy="0 0 0" />
      <mass value="0.227882111375496" />
      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
    </inertial>
    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
  </link>
  <joint name="ManipulatorLink3Joint" type="revolute">
    <origin xyz="-0.012962 0.55415 0" rpy="0 0 0" />
    <parent link="ManipulatorLink2" />
    <child link="ManipulatorLink3" />
    <axis xyz="0 0 -1" />
    <limit lower="0" upper="1" effort="0" velocity="0" />
  </joint>
  <link name="ManipulatorLink4">
    <inertial>
      <origin xyz="-2.27324754187949E-05 0.0839540654377264 0" rpy="0 0 0" />
      <mass value="0.42934890554545" />
      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
    </inertial>
    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
  </link>
  <joint name="ManipulatorLink4Joint" type="revolute">
    <origin xyz="0 0.008 0.034995" rpy="0 1.5708 0" />
    <parent link="ManipulatorLink3" />
    <child link="ManipulatorLink4" />
    <axis xyz="0 -1 0" />
    <limit lower="-3" upper="3" effort="0" velocity="0" />
  </joint>
  <link name="GripperL">
    <inertial>
      <origin xyz="0.00297778710330867 0.0871448028863351 -0.00986508075006032" rpy="0 0 0" />
      <mass value="0.0398581317877607" />
      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
    </inertial>
    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
  </link>
  <joint name="GripperLJoint" type="prismatic">
    <origin xyz="0.049892 0.090686 -0.0096825" rpy="3.1416 -6.9389E-17 -3.1416" />
    <parent link="ManipulatorLink4" />
    <child link="GripperL" />
    <axis xyz="-1 0 0" />
    <limit lower="-0.03" upper="0" effort="0" velocity="0" />
  </joint>
  <link name="GripperR">
    <inertial>
      <origin xyz="0.00297778710330867 0.0871448028863351 0.00986508075006029" rpy="0 0 0" />
      <mass value="0.0398581317877607" />
      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
    </inertial>
    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
  </link>
  <joint name="GripperRJoint" type="prismatic">
    <origin xyz="-0.049892 0.090686 -0.0096825" rpy="-4.9087E-21 6.9389E-17 1.0613E-16" />
    <parent link="ManipulatorLink4" />
    <child link="GripperR" />
    <axis xyz="1 0 0" />
    <limit lower="0" upper="0.03" effort="0" velocity="0" />
  </joint>
  <link name="Trunk">
    <inertial>
      <origin xyz="1.9082E-17 0.23891 1.3227E-17" rpy="0 0 0" />
      <mass value="27.438" />
      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
    </inertial>
    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
  </link>
  <joint name="TrunkJoint" type="revolute">
    <origin xyz="-0.01423 0.00097293 0.686" rpy="1.5708 0 0" />
    <parent link="Base" />
    <child link="Trunk" />
    <axis xyz="0 -1 0" />
    <limit lower="-1.5" upper="1.5" effort="0" velocity="0" />
  </joint>
  <link name="Torso">
    <inertial>
      <origin xyz="-5.96337908854803E-05 0.239039736167763 6.11490025281825E-17" rpy="0 0 0" />
      <mass value="12.3493829426964" />
      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
    </inertial>
    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
  </link>
  <joint name="TorsoJoint" type="revolute">
    <origin xyz="0 0.45 0" rpy="0 0 0" />
    <parent link="Trunk" />
    <child link="Torso" />
    <axis xyz="0 0 -1" />
    <limit lower="0" upper="1" effort="0" velocity="0" />
  </joint>
  <link name="Neck">
    <inertial>
      <origin xyz="-2.54485853576885E-05 0.0271590293807542 3.30681662608079E-17" rpy="0 0 0" />
      <mass value="0.264426936484469" />
      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
    </inertial>
    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
  </link>
  <joint name="NeckJoint" type="revolute">
    <origin xyz="-0.00017682 0.42056 0" rpy="0 0 0" />
    <parent link="Torso" />
    <child link="Neck" />
    <axis xyz="0 -1 0" />
    <limit lower="-1.57" upper="1.57" effort="0" velocity="0" />
  </joint>
  <link name="Head">
    <inertial>
      <origin xyz="0.00279372413046049 0.114190295410849 1.01047642475649E-16" rpy="0 0 0" />
      <mass value="5.04298545454377" />
      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
    </inertial>
    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
  </link>
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

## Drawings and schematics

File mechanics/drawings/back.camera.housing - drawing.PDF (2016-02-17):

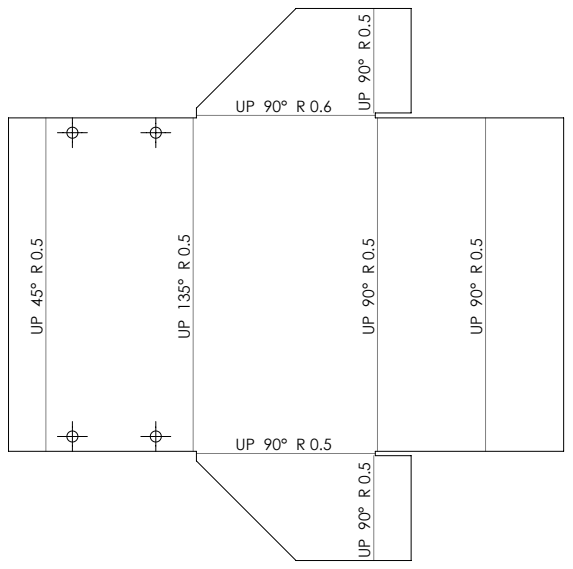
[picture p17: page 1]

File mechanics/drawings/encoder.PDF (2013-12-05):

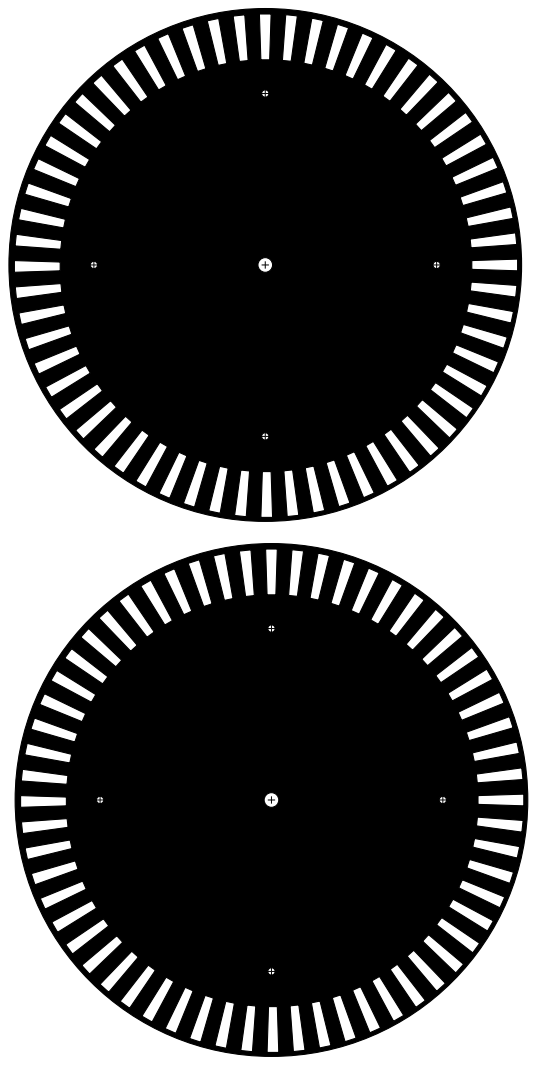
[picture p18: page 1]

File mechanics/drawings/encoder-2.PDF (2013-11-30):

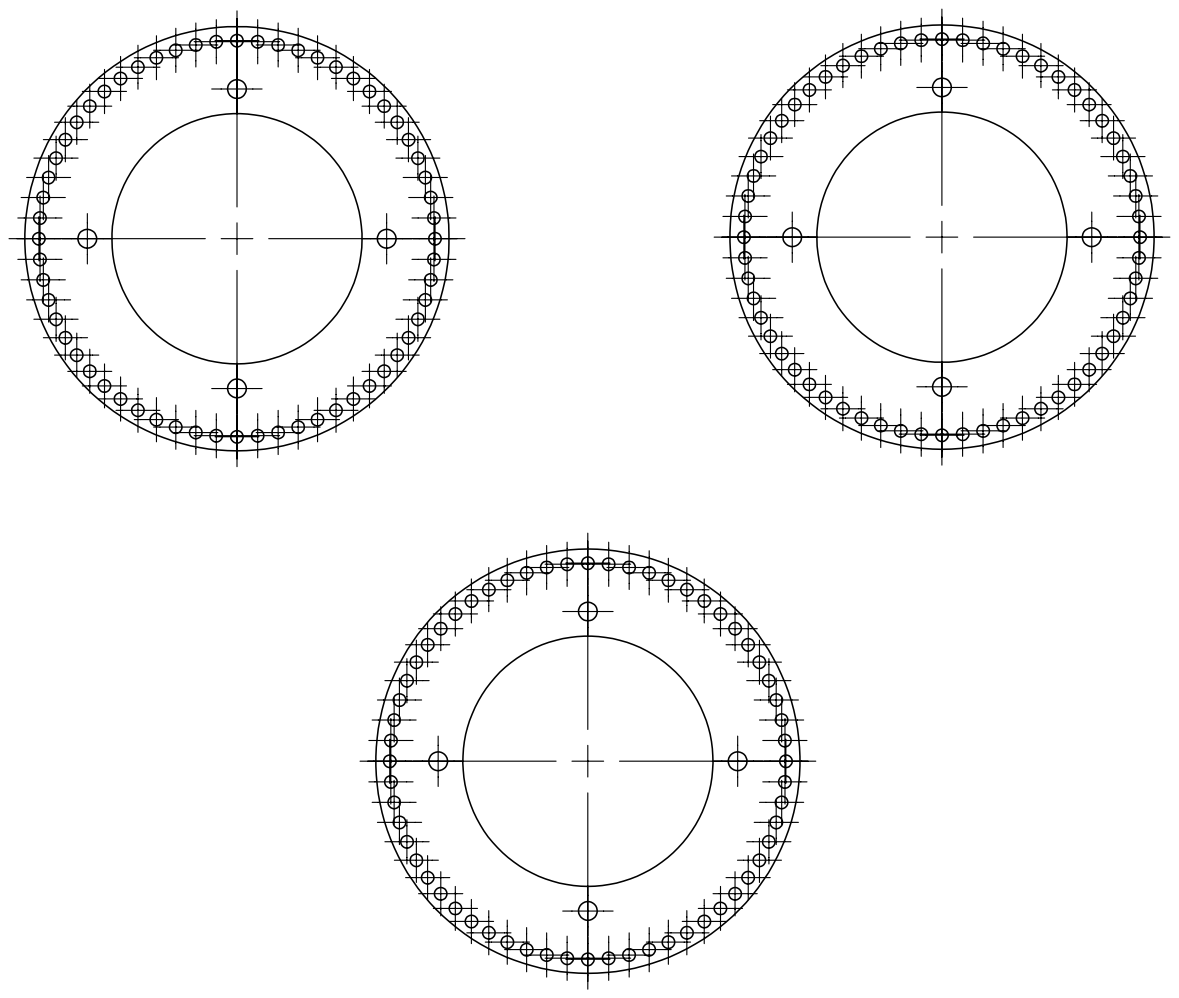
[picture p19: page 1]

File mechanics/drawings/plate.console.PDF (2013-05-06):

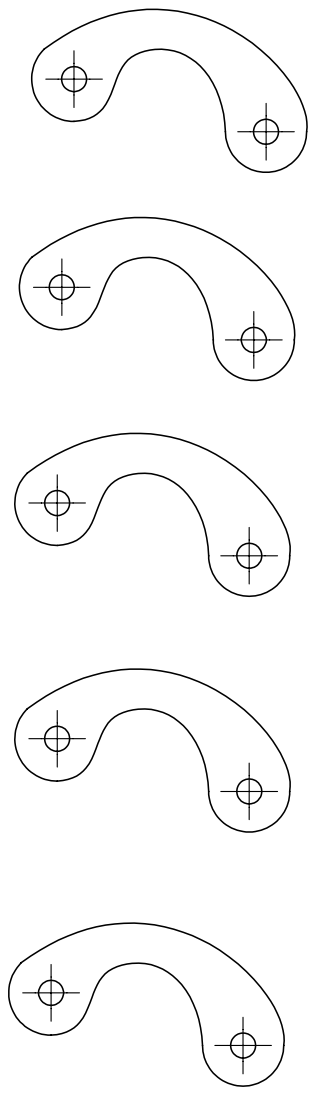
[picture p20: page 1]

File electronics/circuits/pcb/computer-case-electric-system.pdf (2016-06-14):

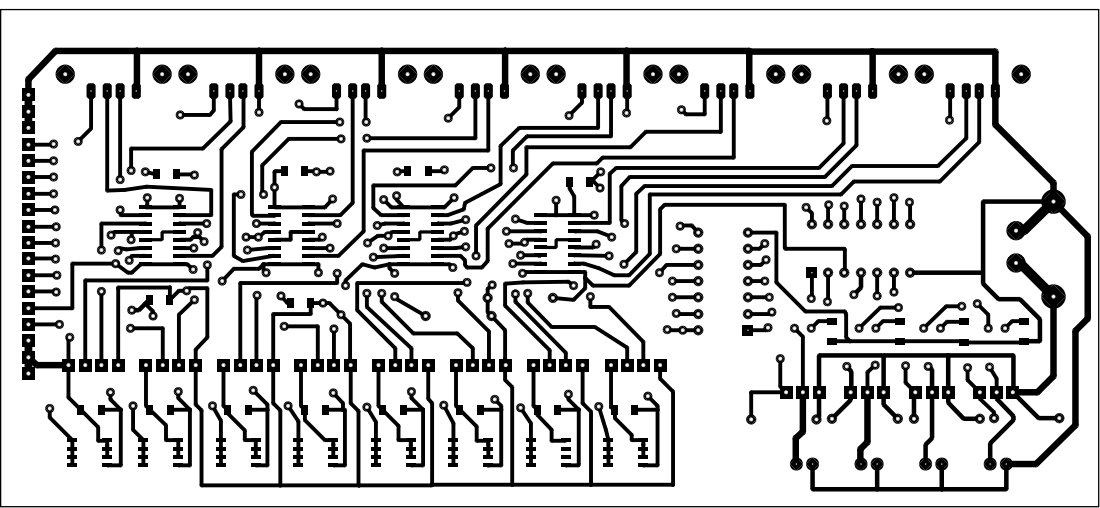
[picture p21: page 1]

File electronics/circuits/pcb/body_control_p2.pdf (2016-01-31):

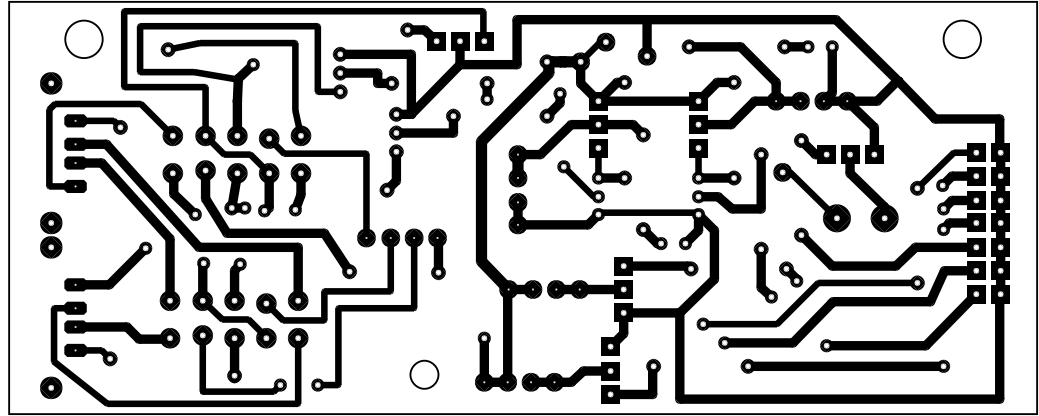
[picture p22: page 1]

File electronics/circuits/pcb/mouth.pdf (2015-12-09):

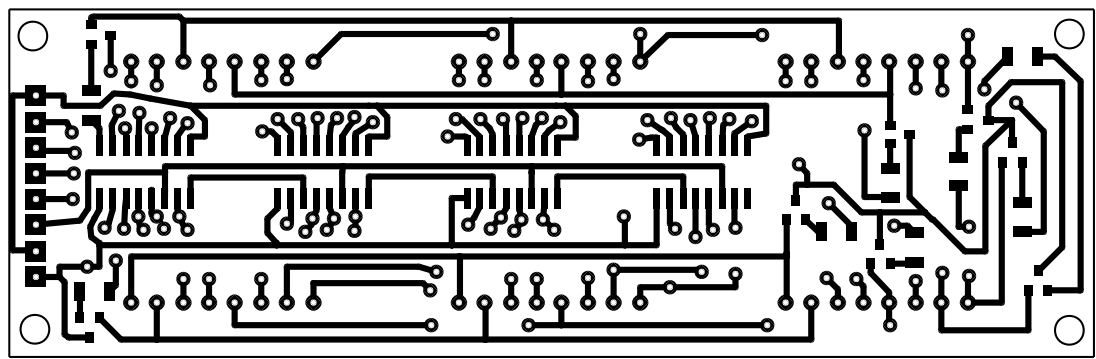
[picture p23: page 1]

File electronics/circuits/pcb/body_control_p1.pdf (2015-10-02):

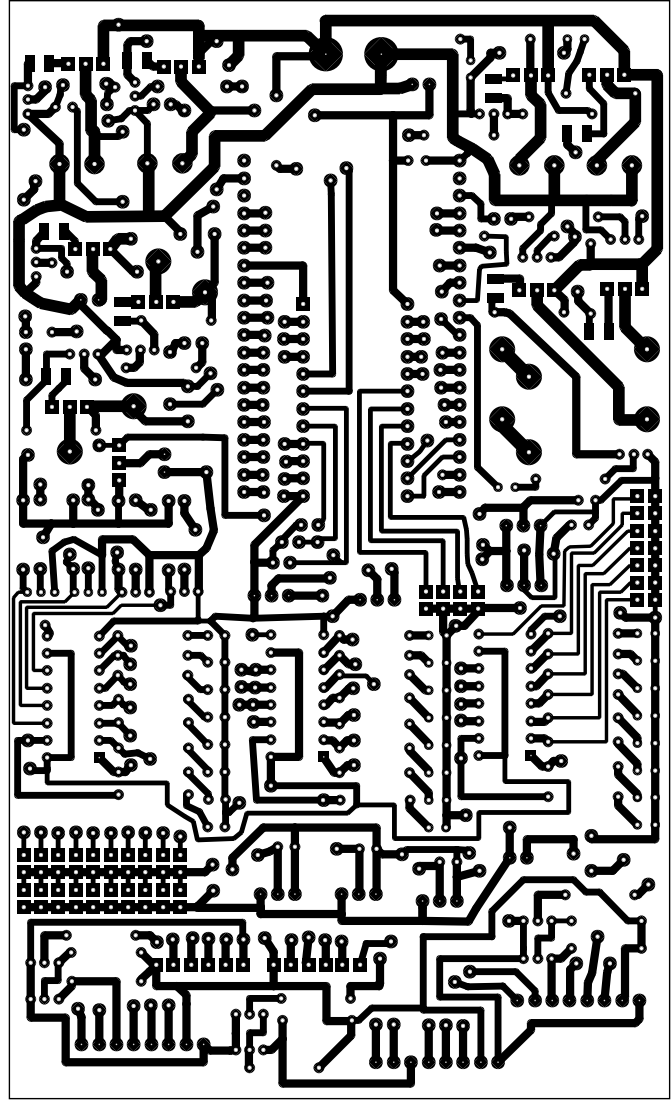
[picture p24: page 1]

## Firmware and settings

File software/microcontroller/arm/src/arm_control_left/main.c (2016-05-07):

#include <stdint.h>
#include <stdio.h>
#include <string.h>
#include <stdlib.h>
#include <math.h>

#include "Board.h"
#include "cdc_enumerate.h"
#include "watchdog.h"
#include "adc.h"
#include "pwm.h"
#include "aic.h"
#include "async.h"
#include "delay.h"
#include "util_math.h"

#include "thresholds.h"

#define FIQ_INTERRUPT_LEVEL 0

unsigned int forearmCCWLimit = 0;
unsigned int forearmCWLimit = 0;

//*----------------------------------------------------------------------------
//* Function Name       : IRQ0Handler
//* Object              : Interrupt Handler called by the IRQ0 interrupt with AT91
//*                       compatibility
//*----------------------------------------------------------------------------
__ramfunc void IRQ0Handler(void)
{
    //forearm.cw.limit
}


//*----------------------------------------------------------------------------
//* Function Name       : IRQ1Handler
//* Object              : Interrupt Handler called by the IRQ1 interrupt with AT91
//*                       compatibility
//*----------------------------------------------------------------------------
__ramfunc void IRQ1Handler(void)
{
    //forearm.ccw.limit
}


//*----------------------------------------------------------------------------
//* Function Name       : FIQHandler
//* Object              : Interrupt Handler called by the FIQ interrupt with AT91
//*                       compatibility
//*----------------------------------------------------------------------------
__ramfunc void FIQHandler(void)
{
    //reserved
}


/*
 *  CDC Functions
 */

struct _AT91S_CDC               pCDC;
//*----------------------------------------------------------------------------
//* function     AT91F_USB_Open
//*              This function Open the USB device
//*----------------------------------------------------------------------------
void AT91FUSBOpen(void)
{
    // Set the PLL USB Divider
    AT91C_BASE_CKGR->CKGR_PLLR |= AT91C_CKGR_USBDIV_1 ;

    // Specific Chip USB Initialization
    // Enables the 48MHz USB clock UDPCK and System Peripheral USB Clock
    AT91C_BASE_PMC->PMC_SCER = AT91C_PMC_UDP;
    AT91C_BASE_PMC->PMC_PCER = (1 << AT91C_ID_UDP);

    // Enable UDP PullUp (USB_DP_PUP) : enable & Clear of the corresponding PIO
    // Set in PIO mode and Configure in Output
    AT91F_PIO_CfgOutput(AT91C_BASE_PIOA, AT91C_PIO_PA16);
    // Clear for set the Pull up resistor
    AT91F_PIO_ClearOutput(AT91C_BASE_PIOA, AT91C_PIO_PA16);

    // CDC Open by structure initialization
    AT91F_CDC_Open(&pCDC, AT91C_BASE_UDP);
}

#define CDC_MSG_SIZE            512

char *msg[CDC_MSG_SIZE];
char *cmd[CDC_MSG_SIZE];
/*
 * Structure to keep CDC message
 */
struct cdcMessage
{
    unsigned char data[CDC_MSG_SIZE];
    unsigned int length;
};

/*
 *  Fill-in CDC Message Structure
 */
struct cdcMessage getCDCMEssage(void)
{
    struct cdcMessage cdcMessageObj;

    for(int r = 0; r < CDC_MSG_SIZE; r++)
    {
        cdcMessageObj.data[r] = '\0';
    }

    cdcMessageObj.length = pCDC.Read(&pCDC, (char *)cdcMessageObj.data, CDC_MSG_SIZE);

    return cdcMessageObj;
}

static void InitPWM(void)
{
    // enable PWM peripherals on PA0, PA1, PA2
    AT91F_PIO_CfgPeriph(AT91C_BASE_PIOA, AT91C_PA0_PWM0, 0);
    AT91F_PIO_CfgPeriph(AT91C_BASE_PIOA, AT91C_PA1_PWM1, 0);
    AT91F_PIO_CfgPeriph(AT91C_BASE_PIOA, AT91C_PA2_PWM2, 0);
    /////////////////////////////////////////////////////////////////////// PWM3 output on PA7 used as PIO
    //AT91F_PIO_CfgPeriph(AT91C_BASE_PIOA, 0, AT91C_PA7_PWM3);
    //AT91F_PIO_CfgPeriph(AT91C_BASE_PIOA, AT91C_PA7_PWM3, 0);

    AT91F_PWMC_InterruptDisable(AT91C_BASE_PWMC, AT91C_PWMC_CHID0);
    AT91F_PWMC_InterruptDisable(AT91C_BASE_PWMC, AT91C_PWMC_CHID1);
    AT91F_PWMC_InterruptDisable(AT91C_BASE_PWMC, AT91C_PWMC_CHID2);
    //AT91F_PWMC_InterruptDisable(AT91C_BASE_PWMC, AT91C_PWMC_CHID3);

    AT91F_PMC_EnablePeriphClock( AT91C_BASE_PMC, 1 << AT91C_ID_PIOA);

    // enable PWM clock in PMC
    AT91F_PWMC_CfgPMC();

    // disable PWM channels 0, 1, 2
    AT91F_PWMC_StopChannel(AT91C_BASE_PWMC, AT91C_PWMC_CHID0);
    AT91F_PWMC_StopChannel(AT91C_BASE_PWMC, AT91C_PWMC_CHID1);
    AT91F_PWMC_StopChannel(AT91C_BASE_PWMC, AT91C_PWMC_CHID2);
    //AT91F_PWMC_StopChannel(AT91C_BASE_PWMC, AT91C_PWMC_CHID3);

    pwmFreqSet(0, 8000);
    pwmFreqSet(1, 8000);
    pwmFreqSet(2, 8000);
    //pwmFreqSet(3, 8000);

    pwmDutySet_u8(0, 1);
    pwmDutySet_u8(1, 1);
    pwmDutySet_u8(2, 1);
    //pwmDutySet_u8(3, 1);

    AT91F_PWMC_UpdateChannel(AT91C_BASE_PWMC, 0, AT91C_PWMC_CHID0);
    AT91F_PWMC_UpdateChannel(AT91C_BASE_PWMC, 1, AT91C_PWMC_CHID1);
    AT91F_PWMC_UpdateChannel(AT91C_BASE_PWMC, 2, AT91C_PWMC_CHID2);
    //AT91F_PWMC_UpdateChannel(AT91C_BASE_PWMC, 3, AT91C_PWMC_CHID3);

    AT91F_PWMC_StopChannel(AT91C_BASE_PWMC, AT91C_PWMC_CHID0);
    AT91F_PWMC_StopChannel(AT91C_BASE_PWMC, AT91C_PWMC_CHID1);
    AT91F_PWMC_StopChannel(AT91C_BASE_PWMC, AT91C_PWMC_CHID2);
    //AT91F_PWMC_StopChannel(AT91C_BASE_PWMC, AT91C_PWMC_CHID3);

    // enable PWM channels 0, 1, 2
    //AT91F_PWMC_StartChannel(AT91C_BASE_PWMC, AT91C_PWMC_CHID0);
    //AT91F_PWMC_StartChannel(AT91C_BASE_PWMC, AT91C_PWMC_CHID1);
    //AT91F_PWMC_StartChannel(AT91C_BASE_PWMC, AT91C_PWMC_CHID2);
    //AT91F_PWMC_StartChannel(AT91C_BASE_PWMC, AT91C_PWMC_CHID3);
}

static void InitPIO(void)
{
    // U1 PIO (hand sensors) configuration (perephirals on valter/electronics/circuits/arm_interface.dsn)
    AT91F_PIO_CfgOutput(AT91C_BASE_PIOA, AT91C_PIO_PA27);   //U1 A
    AT91F_PIO_CfgOutput(AT91C_BASE_PIOA, AT91C_PIO_PA28);   //U1 B
    AT91F_PIO_CfgOutput(AT91C_BASE_PIOA, AT91C_PIO_PA29);   //U1 C
    AT91F_PIO_CfgOutput(AT91C_BASE_PIOA, AT91C_PIO_PA31);   //U1 D

    AT91F_PIO_CfgOutput(AT91C_BASE_PIOA, AT91C_PIO_PA9);    //U2 A
    AT91F_PIO_CfgOutput(AT91C_BASE_PIOA, AT91C_PIO_PA10);   //U2 B
    AT91F_PIO_CfgOutput(AT91C_BASE_PIOA, AT91C_PIO_PA11);   //U2 C
    AT91F_PIO_CfgOutput(AT91C_BASE_PIOA, AT91C_PIO_PA12);   //U2 D

    //hand pitch and yaw drive
    AT91F_PIO_CfgOutput(AT91C_BASE_PIOA, AT91C_PIO_PA3);    //U3.IN1
    AT91F_PIO_CfgOutput(AT91C_BASE_PIOA, AT91C_PIO_PA8);    //U3.IN3
    AT91F_PIO_CfgOutput(AT91C_BASE_PIOA, AT91C_PIO_PA13);   //U3.ENA
    AT91F_PIO_CfgOutput(AT91C_BASE_PIOA, AT91C_PIO_PA14);   //U3.ENB

    //forearm yaw drive
    AT91F_PIO_CfgOutput(AT91C_BASE_PIOA, AT91C_PIO_PA23);   //U4.IN3
    AT91F_PIO_CfgOutput(AT91C_BASE_PIOA, AT91C_PIO_PA22);   //U4.ENB

    //forearm liftup
    AT91F_PIO_CfgOutput(AT91C_BASE_PIOA, AT91C_PIO_PA4);   //U4.IN1
    AT91F_PIO_CfgOutput(AT91C_BASE_PIOA, AT91C_PIO_PA5);   //U4.IN2

    //arm liftup
    AT91F_PIO_CfgOutput(AT91C_BASE_PIOA, AT91C_PIO_PA6);   //U5.IN1
    AT91F_PIO_CfgOutput(AT91C_BASE_PIOA, AT91C_PIO_PA7);   //U5.IN2

    //limb liftup
    AT91F_PIO_CfgOutput(AT91C_BASE_PIOA, AT91C_PIO_PA15);   //U6.IN1
    AT91F_PIO_CfgOutput(AT91C_BASE_PIOA, AT91C_PIO_PA16);   //U6.IN2

    //forearm.roll cnc driver
    AT91F_PIO_CfgOutput(AT91C_BASE_PIOA, AT91C_PIO_PA24);
    AT91F_PIO_CfgOutput(AT91C_BASE_PIOA, AT91C_PIO_PA25);
    AT91F_PIO_CfgOutput(AT91C_BASE_PIOA, AT91C_PIO_PA26);

    //arm leds
    AT91F_PIO_CfgOutput(AT91C_BASE_PIOA, AT91C_PIO_PA21);

    AT91F_PIO_CfgInput(AT91C_BASE_PIOA, AT91C_PIO_PA20);  // IRQ0
    AT91F_PIO_CfgInput(AT91C_BASE_PIOA, AT91C_PIO_PA30);  // IRQ1
    AT91F_PIO_CfgInput(AT91C_BASE_PIOA, AT91C_PIO_PA19);  // FIQ (reserved)

    AT91F_PIO_CfgInput(AT91C_BASE_PIOA, AT91C_PIO_PA17);  // ADC Channel 0
    AT91F_PIO_CfgInput(AT91C_BASE_PIOA, AT91C_PIO_PA18);  // ADC Channel 1

    AT91F_PIO_ClearOutput(AT91C_BASE_PIOA, AT91C_PIO_PA27);
    AT91F_PIO_ClearOutput(AT91C_BASE_PIOA, AT91C_PIO_PA28);
    AT91F_PIO_ClearOutput(AT91C_BASE_PIOA, AT91C_PIO_PA29);
    AT91F_PIO_ClearOutput(AT91C_BASE_PIOA, AT91C_PIO_PA31);
    AT91F_PIO_ClearOutput(AT91C_BASE_PIOA, AT91C_PIO_PA3);
    AT91F_PIO_ClearOutput(AT91C_BASE_PIOA, AT91C_PIO_PA8);
    AT91F_PIO_ClearOutput(AT91C_BASE_PIOA, AT91C_PIO_PA13);
    AT91F_PIO_ClearOutput(AT91C_BASE_PIOA, AT91C_PIO_PA14);
    AT91F_PIO_ClearOutput(AT91C_BASE_PIOA, AT91C_PIO_PA23);
    AT91F_PIO_ClearOutput(AT91C_BASE_PIOA, AT91C_PIO_PA22);
    AT91F_PIO_ClearOutput(AT91C_BASE_PIOA, AT91C_PIO_PA6);
    AT91F_PIO_ClearOutput(AT91C_BASE_PIOA, AT91C_PIO_PA7);
    AT91F_PIO_ClearOutput(AT91C_BASE_PIOA, AT91C_PIO_PA15);
    AT91F_PIO_ClearOutput(AT91C_BASE_PIOA, AT91C_PIO_PA16);
    AT91F_PIO_ClearOutput(AT91C_BASE_PIOA, AT91C_PIO_PA21);
    AT91F_PIO_ClearOutput(AT91C_BASE_PIOA, AT91C_PIO_PA24);
    AT91F_PIO_ClearOutput(AT91C_BASE_PIOA, AT91C_PIO_PA25);
    AT91F_PIO_ClearOutput(AT91C_BASE_PIOA, AT91C_PIO_PA26);



    // disable all pull-ups
    AT91C_BASE_PIOA->PIO_PPUDR = ~0;
}

static void InitIRQ()
{
    // IRQ0 initialization
    AT91F_PIO_CfgPeriph(AT91C_BASE_PIOA, AT91C_PIO_PA20, 0);
    AT91F_AIC_ConfigureIt(AT91C_BASE_AIC, AT91C_ID_IRQ0, AT91C_AIC_PRIOR_HIGHEST, AT91C_AIC_SRCTYPE_EXT_NEGATIVE_EDGE, (void(*)(void)) IRQ0Handler);
    AT91F_AIC_EnableIt(AT91C_BASE_AIC, AT91C_ID_IRQ0);

    // IRQ1 initialization
    AT91F_PIO_CfgPeriph(AT91C_BASE_PIOA, AT91C_PIO_PA30, 0);
    AT91F_AIC_ConfigureIt(AT91C_BASE_AIC, AT91C_ID_IRQ1, AT91C_AIC_PRIOR_HIGHEST, AT91C_AIC_SRCTYPE_EXT_NEGATIVE_EDGE, (void(*)(void)) IRQ1Handler);
    AT91F_AIC_EnableIt(AT91C_BASE_AIC, AT91C_ID_IRQ1);

    // FIQ initialization
    AT91F_PIO_CfgPeriph(AT91C_BASE_PIOA, AT91C_PIO_PA19, 0);
    AT91F_AIC_ConfigureIt(AT91C_BASE_AIC, AT91C_ID_FIQ, FIQ_INTERRUPT_LEVEL, AT91C_AIC_SRCTYPE_EXT_NEGATIVE_EDGE, (void(*)(void)) FIQHandler);
    //AT91F_AIC_EnableIt(AT91C_BASE_AIC, AT91C_ID_FIQ);
}


//*----------------------------------------------------------------------------
//* Function Name       : DeviceInit
//* Object              : Device peripherals initialization
///*----------------------------------------------------------------------------
static void DeviceInit(void)
{
    InitPIO();

    // Enable User Reset and set its minimal assertion to 960 us
    AT91C_BASE_RSTC->RSTC_RMR = AT91C_RSTC_URSTEN | (0x4 << 8) | (unsigned int)(0xA5 << 24);

    // Set-up the PIO
    // First, enable the clock of the PIO and set the LEDs in output
    AT91F_PMC_EnablePeriphClock ( AT91C_BASE_PMC, 1 << AT91C_ID_PIOA );

    // Initialize USB device
    AT91FUSBOpen();
    // Wait for the end of enumeration
    while (!pCDC.IsConfigured(&pCDC));

    InitPIO();
    InitADC();
    InitPWM();
    //InitIRQ();
}

// Specific functions


/*
 * Main Entry Point and Main Loop
 */
int main(void)
{
    watchdogReset();

    unsigned char WDINTENTIONALRESET = 0;

    struct cdcMessage cdcMessageObj;
    unsigned int armSensorsChannel = 0;
    unsigned char armSensorsReadings = 0;
    unsigned int armSensorsReading = 0;

    unsigned int sensorsChannel = 0;
    unsigned char sensorsReadings = 0;
    unsigned int sensorsReading = 0;

    unsigned int forearmLiftUpDriveDuty = 1;
    unsigned int armLiftUpDriveDuty = 1;
    unsigned int limbLiftUpDriveDuty = 1;

    unsigned int forearmLiftUpPositionReading = 0;
    unsigned int armLiftUpPositionReading = 0;
    unsigned int limbLiftUpPositionReading = 0;

    //directions
    unsigned char forearmLiftUpDirection = 2;
    unsigned char armLiftUpDirection = 2;
    //unsigned char limbLiftUpDirection = 0;

    //thresholds
    unsigned int forearmLiftUpPositionThreshold = 90;
    unsigned int armLiftUpPositionThreshold = 750;
    //unsigned int limbLiftUpPositionReading = 0;

    unsigned char forearmLiftUpPositionReadings = 0;
    unsigned char armLiftUpPositionReadings = 0;
    unsigned char limbLiftUpPositionReadings = 0;

    unsigned int forearmRollSpeed = 100;

    unsigned char forearmDirection = 2; // 0 - CW, 1 - CCW
    unsigned char forearmCWLimitReadings = 0;
    unsigned char forearmCCWLimitReadings = 0;
    unsigned int forearmSteps = 0;
    unsigned char forearmStepsReadings = 0;

    //hand
    //watchers
    unsigned char handYawWatch = 0;
    unsigned char handPitchWatch = 0;
    //directions
    unsigned char handYawDirection = 0;     //0 - CW, 1 - CCW
    unsigned char handPitchDirection = 0;   //0 - CW, 1 - CCW
    //thresholds
    unsigned int handYawCWThreshold = 10;
    unsigned int handYawCCWThreshold = 950;
    unsigned int handPitchCWThreshold = 130;
    unsigned int handPitchCCWThreshold = 585;
    //positions
    unsigned int handYawPosition = 0;
    unsigned int handPitchPosition = 0;

    //forearm
    //watchers
    unsigned char forearmYawWatch = 0;
    //directions
    unsigned char forearmYawDirection = 0;      //0 - CW, 1 - CCW
    //thresholds
    unsigned int forearmYawCWThreshold = 15;
    unsigned int forearmYawCCWThreshold = 970;
    //positions
    unsigned int forearmYawPosition = 0;

    //globally watchers on/off
    unsigned char allWatchersOnOff = 1; //1 - on, 0 - off

    DeviceInit();

    watchdogReset();

    //forearm roll off
    AT91F_PIO_SetOutput(AT91C_BASE_PIOA, AT91C_PIO_PA25);

    while (1)
    {
        if (WDINTENTIONALRESET == 0)
        {
            watchdogReset();
        }

        //updating logic variables
        forearmCWLimit = AT91F_PIO_IsInputSet(AT91C_BASE_PIOA, AT91C_PIO_PA20) ? 0 : 1;
        forearmCCWLimit = AT91F_PIO_IsInputSet(AT91C_BASE_PIOA, AT91C_PIO_PA30)? 0 : 1;

        cdcMessageObj = getCDCMEssage();
        if (cdcMessageObj.length > 0)
        {
//            sprintf((char *)msg,"MSG:%s\n", cdcMessageObj.data);
//            pCDC.Write(&pCDC, (char *)msg, strlen((char *)msg));

            char *cmdParts;
            cmdParts = strtok((char*) cdcMessageObj.data, "#" );
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

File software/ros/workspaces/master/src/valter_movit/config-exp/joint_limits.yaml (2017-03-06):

# joint_limits.yaml allows the dynamics properties specified in the URDF to be overwritten or augmented as needed
# Specific joint properties can be changed with the keys [max_position, min_position, max_velocity, max_acceleration]
# Joint limits can be turned off with [has_velocity_limits, has_acceleration_limits]
joint_limits:
  LArmElbowJoint:
    has_velocity_limits: false
    max_velocity: 0
    has_acceleration_limits: false
    max_acceleration: 0
  LArmJoint:
    has_velocity_limits: false
    max_velocity: 0
    has_acceleration_limits: false
    max_acceleration: 0
  LForearmRollJoint:
    has_velocity_limits: false
    max_velocity: 0
    has_acceleration_limits: false
    max_acceleration: 0
  LForearmYawJoint:
    has_velocity_limits: false
    max_velocity: 0
    has_acceleration_limits: false
    max_acceleration: 0
  LHandPitchJoint:
    has_velocity_limits: false
    max_velocity: 0
    has_acceleration_limits: false
    max_acceleration: 0
  LShoulderJoint:
    has_velocity_limits: false
    max_velocity: 0
    has_acceleration_limits: false
    max_acceleration: 0
  LTorsoJoint:
    has_velocity_limits: false
    max_velocity: 0
    has_acceleration_limits: false
    max_acceleration: 0
  ManipulatorLink1Joint:
    has_velocity_limits: false
    max_velocity: 0
    has_acceleration_limits: false
    max_acceleration: 0
  ManipulatorLink2Joint:
    has_velocity_limits: false
    max_velocity: 0
    has_acceleration_limits: false
    max_acceleration: 0
  ManipulatorLink3Joint:
    has_velocity_limits: false
    max_velocity: 0
    has_acceleration_limits: false
    max_acceleration: 0
  ManipulatorLink4Joint:
    has_velocity_limits: false
    max_velocity: 0
    has_acceleration_limits: false
    max_acceleration: 0

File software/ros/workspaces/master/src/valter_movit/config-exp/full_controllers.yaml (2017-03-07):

controller_manager_ns: moveit_simple_controller_manager
controller_list:
  - name: right_arm_controller
    action_ns: joint_trajectory_action
    type: FollowJointTrajectory
    joints: [RTorsoJoint, RShoulderJoint, RArmJoint, RArmElbowJoint, RForearmYawJoint, RForearmRollJoint, RHandPitchJoint]

  - name: right_arm_roll_controller
    action_ns: joint_trajectory_action
    type: FollowJointTrajectory
    joints: [RForearmYawJoint, RForearmRollJoint]

  - name: right_arm_liftup_controller
    action_ns: joint_trajectory_action
    type: FollowJointTrajectory
    joints: [RTorsoJoint, RShoulderJoint, RArmJoint]

  - name: left_arm_controller
    action_ns: joint_trajectory_action
    type: FollowJointTrajectory
    joints: [LTorsoJoint, LShoulderJoint, LArmJoint, LArmElbowJoint, LForearmYawJoint, LForearmRollJoint, LHandPitchJoint]

  - name: left_arm_roll_controller
    action_ns: joint_trajectory_action
    type: FollowJointTrajectory
    joints: [LForearmYawJoint, LForearmRollJoint]

  - name: left_arm_liftup_controller
    action_ns: joint_trajectory_action
    type: FollowJointTrajectory
    joints: [LTorsoJoint, LShoulderJoint, LArmJoint]

  - name: manipulator_controller
    action_ns: joint_trajectory_action
    type: FollowJointTrajectory
    joints: [ManipulatorLink1Joint, ManipulatorLink2Joint, ManipulatorLink3Joint, ManipulatorLink4Joint]

  - name: body_controller
    action_ns: joint_trajectory_action
    type: FollowJointTrajectory
    joints: [TrunkJoint, TorsoJoint]

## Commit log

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2013-04-25 simulations/ sub-folder added to electronics/ directory. lm324 simulation circuit added for revision and further improvements and actualization.
    [lm324.DSN]
2013-04-25 Electronics: AT91SAM7S-DB-L Proteus component created and added to VALTER.LIB; documents and datasheets added to electronics/documents/ folder.
    [AT91SAM7S-DB-L.DSN]
2013-04-25 Platform.p2.dia - modyfied with new sensors blocks. Platform.p1.dia - label corrections.
2013-04-25 Mechanics files were updated when were saved with new SolidWorks.
    [SY42STH47.SLDPRT, head.p1.SLDPRT, head.p4.SLDPRT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]
2013-04-25 VNH2SP30 Motor Driver Proteus model created. electroincs/ folder structure modified. Proteus library files updated. VNH2SP30 Motor Driver documents added. Platform.p2.dia modified (charger sensor add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
    [VNH2SP30-DRIVER.DSN]
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2013-04-26 .gitignore for temp files ussensorboard.DSN Proteus circuit added
    [ussensorboard.DSN]
2013-04-26 Sharp IR GP2D120 mechanical model files added to mechanics/
    [Sharp IR Body.SLDPRT, Sharp IR GP2D120.SLDASM, Sharp IR JST.SLDPRT]
2013-04-26 Sharp IR #GP2D120 Sensor added to the mechanical assembly.
    [Sharp IR Body.SLDPRT, Sharp IR GP2D120.SLDASM]
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2013-05-01 ussensorboard rename file to us_sensor_board cur_sensor_board PCB added
    [energy_system.DSN, us_sensor_board.DSN]
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2013-05-02 Energy system circuit initial commit. ILR3705N and BDX53C Proteus simulations. Documents for transistors added.
    [BDX53C.DSN, ILR3705.DSN, energy_system.DSN]
2013-05-03 minor energy system corrections
    [energy_system.DSN]
2013-05-03 mechanical SolidWorks model editions (computer box added, IR sensors added, US sensors added, openings to the platform added)
    [Sharp IR GP2D120.SLDASM, Sharp IR JST.SLDPRT, bottom.SLDPRT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]
2013-05-04 mechanics additions (charger, back wall sensors, computer box)
    [Sharp IR GP2D120.SLDASM, accumulator.5Ah.SLDPRT, accumulator.charger.sm1236.SLDPRT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]
2013-05-04 mechanics additions: charger, dc-dc-12-24, us sensor boards; documents for dc-dc-12-5
    [DC-DC-12-24-fixture-p1.SLDPRT, DC-DC-12-24-fixture-p2.SLDPRT, DC-DC-12-24-fixture.SLDPRT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]
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2013-05-07 mechanics: minor corrections
    [body.cover-for drawing.SLDPRT, body.cover.SLDPRT]
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2013-05-12 electronics: IRL3705N switch correction
2013-05-14 electronics: energy system updated with new IRL3705N switch; IRL3705N switch lib component added; SM1236 inverter charger added.
    [IRL3705N-SWITCH.DSN, SM-1236.DSN, energy_system.DSN]
2013-05-14 electronics: SM 1236 charger module added to energy system circuitry
    [energy_system.DSN]
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2013-05-15 electronics: small accumulators switch added; energy system circuitry modified; lib components added
    [energy_system.DSN, small_accumulator_switch.DSN, small_accumulators_switch_and_cur_sensor.DSN]
2013-05-15 electronics: folder restructure; small accum switch board design in progress
    [small_accumulators_switch_and_cur_sensor.DSN]
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2013-05-16 mechanics: 12V acdc power supply model added; 220V filter extender model added
    [acdc.12v.power.supply.SLDPRT, acdc.220V.filter.SLDPRT]
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2013-05-17 mechanics: ac 220V filter added; ac-dc-12V power supply added
    [AC-DC-12-fixture.SLDPRT]
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2013-05-20 electornics: platform control P1 board (circuit) added (initial commit); cd4067 multiplexer pcb footprint changed
    [AT91SAM7S-DB-L-PCB.DSN, CD4067.DSN, energy_system.DSN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]
2013-05-20 electronics: folders reorganization; platform control p1 improved; level shifter from 3.3V to 5V in progress
    [2n3904_level_shifter.DSN, acs756_cur_sensor_circuit.DSN, energy_system.DSN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]
2013-05-21 electronics: platform control p1 modified (100nF capacitors added)
    [platform_control_p1.DSN]
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2013-05-22 electronics: energy system DCDC5V enebling added; platform control p1 modified by adding free pins terminals
    [energy_system.DSN, platform_control_p1.DSN]
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2013-05-22 electornics: AT91SAM7S PCB footprint minor fix
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2013-05-24 electronics: platform control p1 PCB done with small fixes
    [platform_control_p1.DSN]
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2013-05-24 electronics: platform control p1 fan control added controlled from PWM of each platfrom motor
    [2n3904.DSN, 2n3904_level_shifter.DSN, pc817.DSN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]
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2013-06-04 software:computer:server:core:socket simple example with multiprocess socket server and simple socket client added; minor fix to daemon
2013-06-16 software:microcontroller:arm skeleton program minor fix
    [main.c]
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2013-06-16 soft:mc:arm:skeleton minor fix
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2013-07-14 electronics: platform location circuit digital pot added to models; lm317 added to the schema
    [CAT5111.DSN, lm317-full.DSN, platform_location_p1.DSN]
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2013-07-16 electronics:circuits 74HC595 docs added; platform location supplemented with US sensors output bus; 40kHz input for US board in development.
    [74HC595_24_leds.DSN, platform_location_p1.DSN]
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2013-07-20 electronics:circuits platform location p1 PCB initial commit; check CD4067 to transfer own VCC as a signal.
    [platform_location_p1.DSN]
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2013-07-24 electornics:circuits platform location p1 minor fix (R31 should be short circuited)
    [cd4067_pc847.DSN, platform_location_p1.DSN]
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2013-08-08 soft:mc:arm labels minor fix
    [main.c]
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2013-08-11 soft:mc:arm minor code formatting fix
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2013-08-14 soft:mc:arm platform_location_p1 SERVO control added; platform_control_p1 - TODO added: replace with pwm.h functions
    [main.c]
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2013-09-03 electronics: platform manipulator and ir bumper ~50% components plaement for pcb done
    [platform_manipulator_and_ir_bumper.DSN]
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2013-09-04 electronics: platform manipulator and ir bumper pcb done; to be checked before printing
    [platform_manipulator_and_ir_bumper.DSN]
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2013-10-30 soft:mc:arm platform_manipulator_and_ir_bumper minor fix for dummy commit primarily
    [main.c]
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2013-11-04 soft:mc:platform_manipluator_and_ir_bumper SERIAL DEMO added; some CDC txt commands reversed
    [main.c]
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2013-11-05 soft:mc:arm platform_manipulator_and_ir_bumper improvements and fixes
    [main.c]
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2013-11-05 manipulator: gripper thresholds fixed
    [main.c]
2013-11-06 manipulator: serial demo fixes
    [main.c]
2013-11-07 soft:mc:arm paltform_manipulator_and_ir_bumper DEMO functions fixed (getDynamicDutyVal)
    [main.c]
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2013-11-25 turret position val fix
    [main.c]
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2013-11-27 turret breakage preventing by position
    [main.c]
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2014-01-14 mechanics: charger module finished (except cable inlet tail); servo SM-S3317S model added
    [charger.module.SLDASM, charger.module.aluminum.base.SLDPRT, charger.module.cable.inlet.nut.SLDPRT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]
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2014-04-18 electronics:circuits:platform_control_p2 - some outputs are reassigned, PCB-PHOTO od platform_control_p2 added; software:microcontroller:arm platform_control_p2 pin assignments are changed
    [platform_control_p2.dsn]
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2014-05-06 mechanics: finger pad fixture added
    [finger.pad.SLDPRT]
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2014-05-26 gb08m2: software, firmware and mechanical fixes (lamps were shorted to the ground by their metal cases)
    [main.c]
2014-05-26 gb08m2: reset servo added
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2014-05-31 gb-08-m2: RESET command returns control to main()
    [main.c]
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2014-06-05 gb-08-m2: IR range finder fixes and modifications
    [main.c]
2014-06-13 gb08m2: folder renaming; delay_ms(500) when direction is changed set to 50 ms to prevent lag
    [main.c]
2014-06-13 gb08m2: main_board ARM FW update (shorteting commands)
    [main.c]
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2014-06-16 gb08m2: motors commands shortening
    [main.c]
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2014-07-03 gb08m2: minor template match (camera resolution fix)
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2015-06-12 electronics: arm servos helper board (pcb corrections)
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2015-07-10 electronics: arm_control_p1 fix
    [arm_control_p1.dsn]
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2015-12-07 electronics: mouth LED matrix board rebuild (due to the error)
    [mouth.DSN, mouth_inv.DSN]
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2016-01-18 soft:mc:arm body_control_p1 - left and arm drive duty error fixed
    [main.c]
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2016-03-09 soft:mc and computer: WD reset added to Body Control P1; Qt client singletons added for platform-manipulator-and-ir bumper and for body-control-p1
    [main.c]
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2016-03-26 soft:computer Qt client (detached frames fixed)
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2016-04-05 SW Valter's simplified model minor fix (trunk color)
    [valter.SLDASM]
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2016-04-13 minor fixes; day of initial tests Qt client + Valter
    [main.c]
2016-04-14 software: after testing fixes (PLATFORM-CONTROL-P1 and PLATFORM-LOCATION-P1); PLATFORM-CONTROL-P2 and PLATFORM-MANIPULATOR-AND-IR-BUMPER advanced and ready for preliminary testing;
    [main.c]
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2016-04-19 qt client: man link1 link2 motor control fixed (needs test)
    [main.cpp]
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2016-05-18 Qt client: ARM-CONTROL-LEFT/RIGHT hand sensors readings conflict fixed
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2016-05-20 Qt Client ARM-CONTROL-RIGHT fingers fixes
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2016-05-21 Qt client fingers controls (fixed layout, calls of sub added)
2016-05-21 Qt client: fingers layout fix
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2016-05-23 Qt client fingers coloring RGB out of range assumed fixed
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2016-07-31 qt client: double free or corruption (static variable reassigned too fast)
    [main.cpp]
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2017-03-13 expclient: arm-control-left noise suppress programmatically
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2017-03-15 arm control left - noise supperssors added to Limg and Forearm
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2017-04-05 rpi3: WiringPI resolver webpage
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2017-06-04 expclient: fixing Head Yaw and Pitch...
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2017-06-17 expclient: Left Arm Roll activation button bug fix
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2017-10-27 expclient: PLATFORM-CONTROL-P2 initial servo reset
2017-10-27 expclient: PLATFORM-CONTROL-P2 initial servo reset; threaded
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2021-11-02 expclient TCP Interface fixes
    [main.cpp]
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2024-08-24 Reset body camera from Android App
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
